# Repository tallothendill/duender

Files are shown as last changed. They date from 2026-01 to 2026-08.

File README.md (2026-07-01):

<!-- Improved compatibility of back to top link: See: https://github.com/othneildrew/Best-README-Template/pull/73 -->

<!--
*** Thanks for checking out the Best-README-Template. If you have a suggestion
*** that would make this better, please fork the repo and create a pull request
*** or simply open an issue with the tag "enhancement".
*** Don't forget to give the project a star!
*** Thanks again! Now go create something AMAZING! :D
-->

<!-- PROJECT SHIELDS -->
<!--
*** I'm using markdown "reference style" links for readability.
*** Reference links are enclosed in brackets [ ] instead of parentheses ( ).
*** See the bottom of this document for the declaration of the reference variables
*** for contributors-url, forks-url, etc. This is an optional, concise syntax you may use.
*** https://www.markdownguide.org/basic-syntax/#reference-style-links
-->
<!--
[![Contributors][contributors-shield]][contributors-url]
[![Forks][forks-shield]][forks-url]
[![Stargazers][stars-shield]][stars-url]
[![Issues][issues-shield]][issues-url]
[![Unlicense License][license-shield]][license-url]
[![LinkedIn][linkedin-shield]][linkedin-url]
-->

<!-- PROJECT LOGO -->
<br />
<div align="center">
  <a href="https://www.printables.com/model/1300968-duender-mgn9h-2x-creality-ender-3-corexy-convertio">
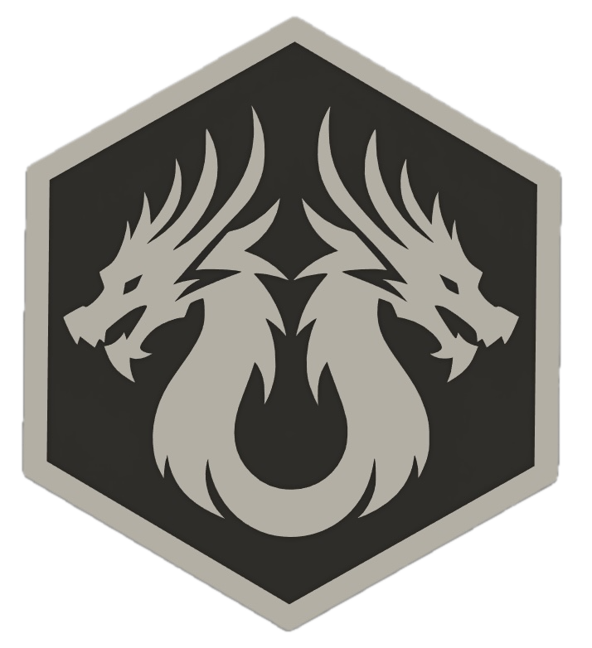
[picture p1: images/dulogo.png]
    
  </a>

  <h3 align="center">Duender mods, triple Z and more...</h3>
  <p align="center">
    Some thougths and mods for the duender project here.
    <br />Note: this is NOT an official repo, Irbis3D repo is <a href="https://github.com/Irbis3D">HERE</a>. Thanks.
  </p>
  <p>
    The Duender project is created and developped by Irbis3D <a href="https://discord.com/channels/1341676245171048473/1354698746524598312">Discord server</a>
  </p>
    <!--
    <br />
    <br />
    <a href="https://github.com/tallothendill/duender/tree/71d104ec3dbbbacea63be96e859a8f34e3e835fc/Kinematic%203Z%20-%20in%20progress">Triple Z axis, with kinematic bed</a>
    </p>X
    &middot;
    <a href="https://github.com/tallothendill/duender/tree/c5b984b065c5a199969d3fe1e7d17b98502cc63b/mods">Mods & stl related to the duender manual</a>
    &middot;
    <a href="https://github.com/othneildrew/Best-README-Template/issues/new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">Request Feature</a>
  </p>
</div>
-->

<!-- TABLE OF CONTENTS -->

<!--
<details>
  <summary>Table of Contents</summary>
  <ol>
    <li>
      <a href="#about-the-project">About The Project</a>
      <ul>
        <li><a href="#built-with">Built With</a></li>
      </ul>
    </li>
    <li>
      <a href="#getting-started">Getting Started</a>
      <ul>
        <li><a href="#prerequisites">Prerequisites</a></li>
        <li><a href="#installation">Installation</a></li>
      </ul>
    </li>
    <li><a href="#usage">Usage</a></li>
    <li><a href="#roadmap">Roadmap</a></li>
    <li><a href="#contributing">Contributing</a></li>
    <li><a href="#license">License</a></li>
    <li><a href="#contact">Contact</a></li>
    <li><a href="#acknowledgments">Acknowledgments</a></li>
  </ol>
</details>
-->

<!-- ABOUT THE PROJECT -->
<!--
## About The Project

[![Product Name Screen Shot][product-screenshot]](https://example.com)

There are many great README templates available on GitHub; however, I didn't find one that really suited my needs so I created this enhanced one. I want to create a README template so amazing that it'll be the last one you ever need -- I think this is it.

Here's why:
* Your time should be focused on creating something amazing. A project that solves a problem and helps others
* You shouldn't be doing the same tasks over and over like creating a README from scratch
* You should implement DRY principles to the rest of your life :smile:

Of course, no one template will serve all projects since your needs may be different. So I'll be adding more in the near future. You may also suggest changes by forking this repo and creating a pull request or opening an issue. Thanks to all the people have contributed to expanding this template!

Use the `BLANK_README.md` to get started.

<p align="right">(<a href="#readme-top">back to top</a>)</p>

### Built With

This section should list any major frameworks/libraries used to bootstrap your project. Leave any add-ons/plugins for the acknowledgements section. Here are a few examples.

* [![Next][Next.js]][Next-url]
* [![React][React.js]][React-url]
* [![Vue][Vue.js]][Vue-url]
* [![Angular][Angular.io]][Angular-url]
* [![Svelte][Svelte.dev]][Svelte-url]
* [![Laravel][Laravel.com]][Laravel-url]
* [![Bootstrap][Bootstrap.com]][Bootstrap-url]
* [![JQuery][JQuery.com]][JQuery-url]

<p align="right">(<a href="#readme-top">back to top</a>)</p>
-->

<!-- GETTING STARTED -->
<!--
## Getting Started

This is an example of how you may give instructions on setting up your project locally.
To get a local copy up and running follow these simple example steps.

### Prerequisites

This is an example of how to list things you need to use the software and how to install them.
* npm
  ```sh
  npm install npm@latest -g
  ```

### Installation

_Below is an example of how you can instruct your audience on installing and setting up your app. This template doesn't rely on any external dependencies or services._

1. Get a free API Key at [https://example.com](https://example.com)
2. Clone the repo
   ```sh
   git clone https://github.com/github_username/repo_name.git
   ```
3. Install NPM packages
   ```sh
   npm install
   ```
4. Enter your API in `config.js`
   ```js
   const API_KEY = 'ENTER YOUR API';
   ```
5. Change git remote url to avoid accidental pushes to base project
   ```sh
   git remote set-url origin github_username/repo_name
   git remote -v # confirm the changes
   ```

<p align="right">(<a href="#readme-top">back to top</a>)</p>
-->

<!-- USAGE EXAMPLES -->
<!--
## Usage

Use this space to show useful examples of how a project can be used. Additional screenshots, code examples and demos work well in this space. You may also link to more resources.

_For more examples, please refer to the [Documentation](https://example.com)_

<p align="right">(<a href="#readme-top">back to top</a>)</p>
-->

<!-- ROADMAP -->
<!--
## Roadmap

- [x] Add Changelog
- [x] Add back to top links
- [ ] Add Additional Templates w/ Examples
- [ ] Add "components" document to easily copy & paste sections of the readme
- [ ] Multi-language Support
    - [ ] Chinese
    - [ ] Spanish

See the [open issues](https://github.com/othneildrew/Best-README-Template/issues) for a full list of proposed features (and known issues).

<p align="right">(<a href="#readme-top">back to top</a>)</p>
-->

<!-- CONTRIBUTING -->
<!--
## Contributing

Contributions are what make the open source community such an amazing place to learn, inspire, and create. Any contributions you make are **greatly appreciated**.

If you have a suggestion that would make this better, please fork the repo and create a pull request. You can also simply open an issue with the tag "enhancement".
Don't forget to give the project a star! Thanks again!

1. Fork the Project
2. Create your Feature Branch (`git checkout -b feature/AmazingFeature`)
3. Commit your Changes (`git commit -m 'Add some AmazingFeature'`)
4. Push to the Branch (`git push origin feature/AmazingFeature`)
5. Open a Pull Request

### Top contributors:

<a href="https://github.com/othneildrew/Best-README-Template/graphs/contributors">
  <img src="https://contrib.rocks/image?repo=othneildrew/Best-README-Template" alt="contrib.rocks image" />
</a>

<p align="right">(<a href="#readme-top">back to top</a>)</p>
-->

<!-- LICENSE -->
<!--
## License

Distributed under the Unlicense License. See `LICENSE.txt` for more information.

<p align="right">(<a href="#readme-top">back to top</a>)</p>
-->

<!-- CONTACT -->
<!--
## Contact

Your Name - [@your_twitter](https://twitter.com/your_username) - email@example.com

Project Link: [https://github.com/your_username/repo_name](https://github.com/your_username/repo_name)

<p align="right">(<a href="#readme-top">back to top</a>)</p>
-->

<!-- ACKNOWLEDGMENTS -->
<!--
## Acknowledgments

Use this space to list resources you find helpful and would like to give credit to. I've included a few of my favorites to kick things off!

* [Choose an Open Source License](https://choosealicense.com)
* [GitHub Emoji Cheat Sheet](https://www.webpagefx.com/tools/emoji-cheat-sheet)
* [Malven's Flexbox Cheatsheet](https://flexbox.malven.co/)
* [Malven's Grid Cheatsheet](https://grid.malven.co/)
* [Img Shields](https://shields.io)
* [GitHub Pages](https://pages.github.com)
* [Font Awesome](https://fontawesome.com)
* [React Icons](https://react-icons.github.io/react-icons/search)

<p align="right">(<a href="#readme-top">back to top</a>)</p>
-->

<!-- MARKDOWN LINKS & IMAGES -->
<!-- https://www.markdownguide.org/basic-syntax/#reference-style-links -->
<!--
[contributors-shield]: https://img.shields.io/github/contributors/othneildrew/Best-README-Template.svg?style=for-the-badge
[contributors-url]: https://github.com/othneildrew/Best-README-Template/graphs/contributors
[forks-shield]: https://img.shields.io/github/forks/othneildrew/Best-README-Template.svg?style=for-the-badge
[forks-url]: https://github.com/othneildrew/Best-README-Template/network/members
[stars-shield]: https://img.shields.io/github/stars/othneildrew/Best-README-Template.svg?style=for-the-badge
[stars-url]: https://github.com/othneildrew/Best-README-Template/stargazers
[issues-shield]: https://img.shields.io/github/issues/othneildrew/Best-README-Template.svg?style=for-the-badge
[issues-url]: https://github.com/othneildrew/Best-README-Template/issues
[license-shield]: https://img.shields.io/github/license/othneildrew/Best-README-Template.svg?style=for-the-badge
[license-url]: https://github.com/othneildrew/Best-README-Template/blob/master/LICENSE.txt
[linkedin-shield]: https://img.shields.io/badge/-LinkedIn-black.svg?style=for-the-badge&logo=linkedin&colorB=555
[linkedin-url]: https://linkedin.com/in/othneildrew
[product-screenshot]: images/screenshot.png
[Next.js]: https://img.shields.io/badge/next.js-000000?style=for-the-badge&logo=nextdotjs&logoColor=white
[Next-url]: https://nextjs.org/
[React.js]: https://img.shields.io/badge/React-20232A?style=for-the-badge&logo=react&logoColor=61DAFB
[React-url]: https://reactjs.org/
[Vue.js]: https://img.shields.io/badge/Vue.js-35495E?style=for-the-badge&logo=vuedotjs&logoColor=4FC08D
[Vue-url]: https://vuejs.org/
[Angular.io]: https://img.shields.io/badge/Angular-DD0031?style=for-the-badge&logo=angular&logoColor=white
[Angular-url]: https://angular.io/
[Svelte.dev]: https://img.shields.io/badge/Svelte-4A4A55?style=for-the-badge&logo=svelte&logoColor=FF3E00
[Svelte-url]: https://svelte.dev/
[Laravel.com]: https://img.shields.io/badge/Laravel-FF2D20?style=for-the-badge&logo=laravel&logoColor=white
[Laravel-url]: https://laravel.com
[Bootstrap.com]: https://img.shields.io/badge/Bootstrap-563D7C?style=for-the-badge&logo=bootstrap&logoColor=white
[Bootstrap-url]: https://getbootstrap.com
[JQuery.com]: https://img.shields.io/badge/jQuery-0769AD?style=for-the-badge&logo=jquery&logoColor=white
[JQuery-url]: https://jquery.com 
-->

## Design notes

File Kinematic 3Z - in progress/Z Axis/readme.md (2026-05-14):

<p>
  Aligned the Lead screw axis with the GE5C bearing axis to eliminate torque creation while moving.
  <br />The screw must create the movement, the rail is only a guide, the GE5C is only carrying the weight of the bed vertically.
</p>

<p>The most important point in building this is to give the bed holders some degrees of freedom:
<ul>
  Front left holder to front bed extrusion:
    <li>No freedom, act as a reference point</li>
    <li>Have the two M5 screw/M5T-nut secured so the holder does not move in X, Y or Z</li>
</ul>
<ul>
  Front right holder to front bed extrusion:
  <li>Allows for movement in X axis</li>
  <li>This allows for the bed to tilt laterally, and for X axis thermal expansion without forcing the bed to warp under stress</li>
  <li>The screws must be tight to the point where there is no more Z rattling, but the T-nuts still slide into the extrusion channel</li>
</ul>
<ul>
  Back support to back bed extrusion:
    <li>Allows for movement both in X and Y axis</li>
    <li>This allows for the bed to tilt front to back, and therml expansion without Y axis stress</li>
    <li>Here also, the screws must be tightened just enough to eliminate any rattling in Z direction, but still slide laterally in the extrusion channel and also on the Y axis (the support should &quot;glide&quot; onto the extrusion a few 0.x mm)</li>
</ul>
</p>
<p>
  A good way to &quot;calibrate&quot; screw torques is to tighten them to contact, then, while manually making the bed tilt back and forth, tightening/loosening by 1/8 turn until it feels just right: the bed should tilt every direction without notable resistance point.
</p>

<p>
  Any comments or improvements are welcome at:<br />
 <a target="_blank" href="https://discord.com/channels/1341676245171048473/1451586393146003507">B&W ender MGN9H build log on Discord</a>
</p>

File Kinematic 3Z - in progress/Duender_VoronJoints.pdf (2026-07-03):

## Blind joints “a la Voron“ ADDON ⁻ All versions

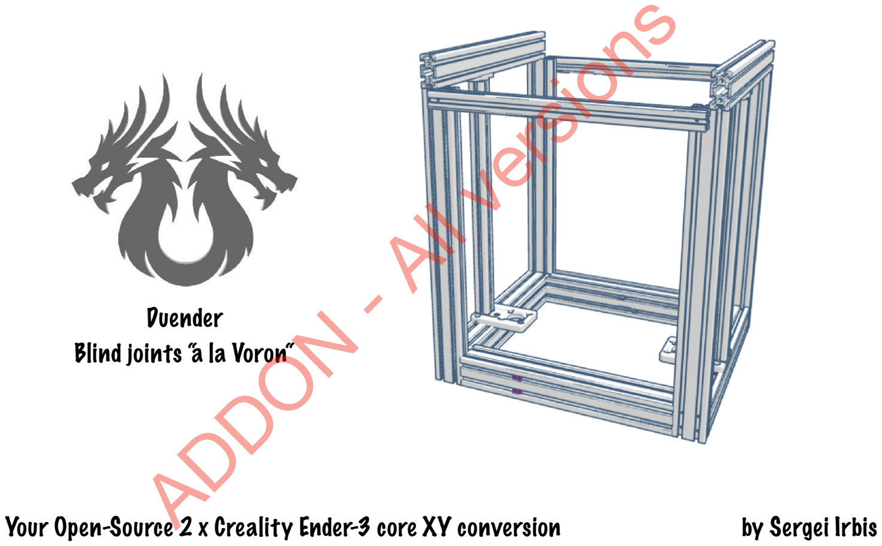
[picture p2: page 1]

## Duender

Your Open-Source 2 x Creality Ender-3 core XY conversion | by Sergei Irbis

## Caution!

For this method to work, the cuts on your extrusions must be perfectly square with their body.
If the cut is not 90°, the assembly cannot end square!
You can somewhat compensate with a shim where needed, but this solution has its limits, plus it may create unwanted gaps between your extrusions.

two printed parts to help with the process:

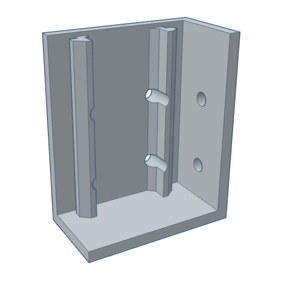
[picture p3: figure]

A simple drilling jig, to place the holes without too much thinking.
Many models exist online, some even with bearings to guide you.

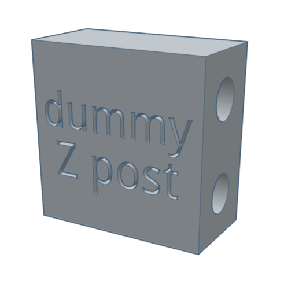
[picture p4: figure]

A 40x40x20mm dummy to fill the space of 2040 vertical extrusions.
Its holes allow for two M5x45 SHCS Ender 3 screws to secure it onto 4040 extrusions sides.

TOOLS YOU’LL NEED:

2mm Allen key

A drill, I went with a 4,2mm bit, but if you are precise enough, 4mm should be fine.
Note that a drill press will make things way easier, as it is important to drill straight and square into the extrusions.

A M5 tap, along with its handle, and some lubricant to cut the threads into the extrusions channels.

Base structure | 6

## Assembling the frame

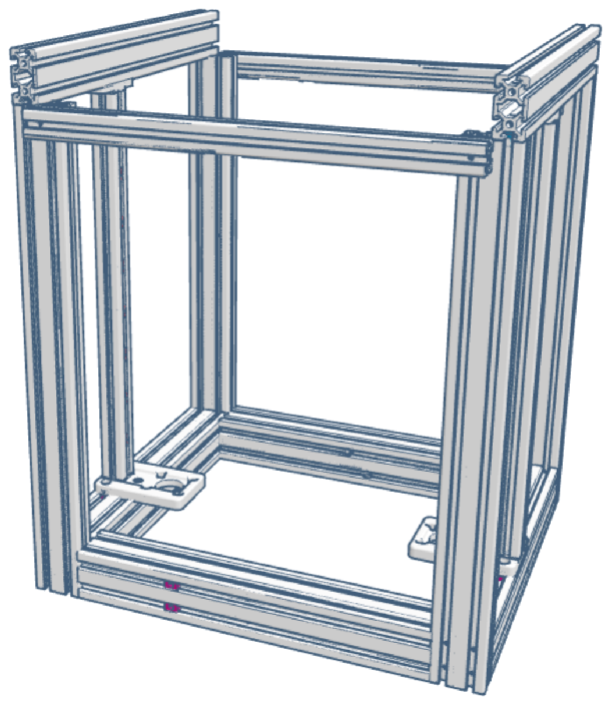
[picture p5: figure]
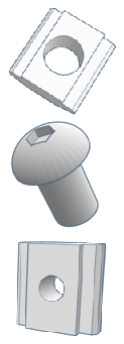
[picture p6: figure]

M5 T-slot nut | 18
M5x8 BHCS screw | 54
M3 T-slot nut | 16

Base structure | 7

2020-D *

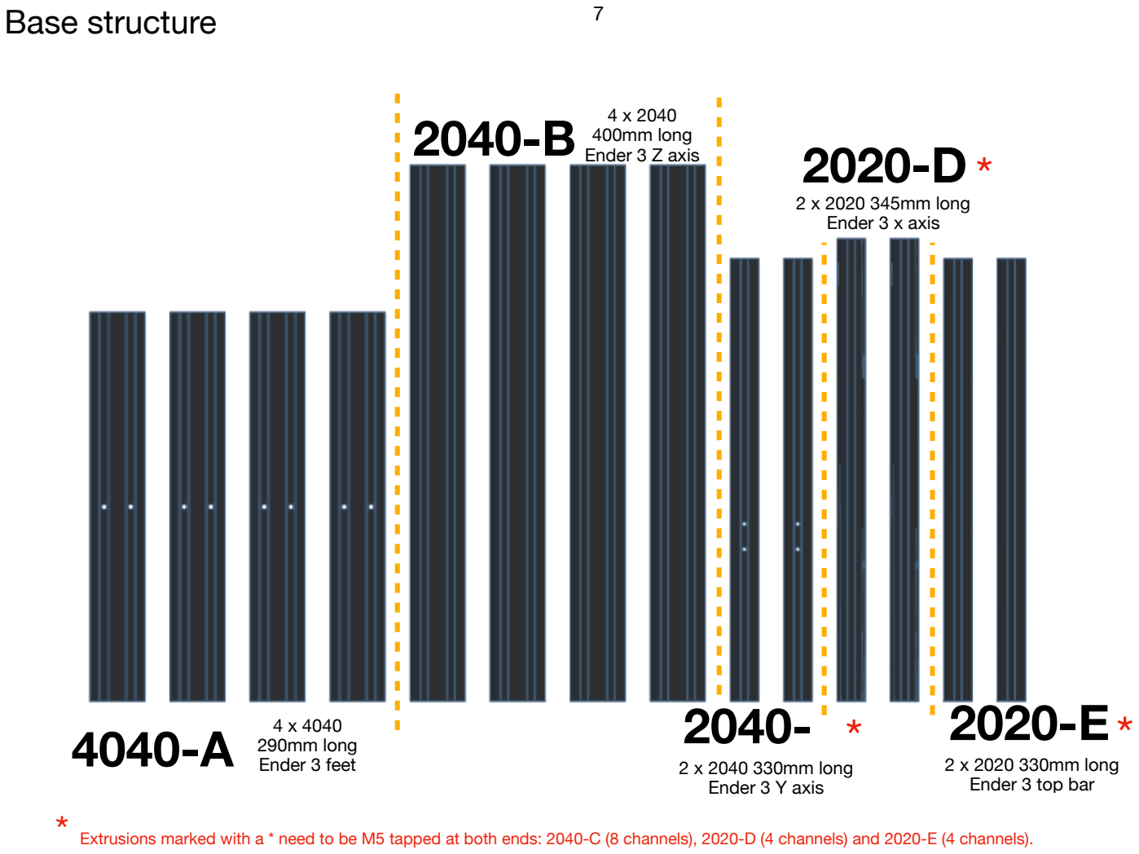
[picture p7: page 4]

4 x 2040
400mm long 2040-B Ender 3 Z axis

4 x 4040
290mm long 4040-A Ender 3 feet | 2 x 2040 330mm long
| Ender 3 Y axis

2040- *

2 x 2020 345mm long
Ender 3 x axis

2 x 2020 330mm long
Ender 3 top bar

2020-E*

* Extrusions marked with a * need to be M5 tapped at both ends: 2040-C (8 channels), 2020-D (4 channels) and 2020-E (4 channels).

Base structure | 8

Drill the 400mm 2040 Z posts bases
2 holes in the 20mm side, 4 holes in the 40mm face.

Bottom holes have their centre at 10mm from the base, Top holes are centred at 30mm from the base.

Of course, all are centred on the extrusions channels. Be precise when marking or centre-punching those.

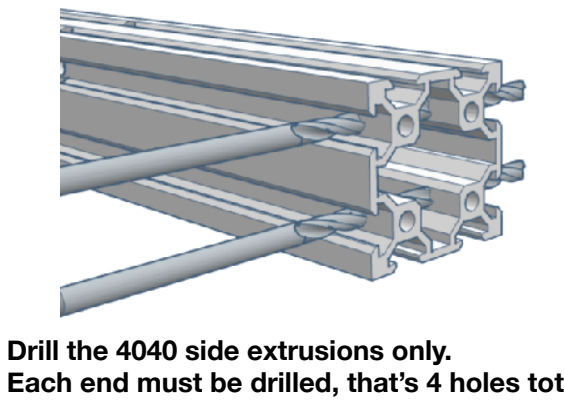
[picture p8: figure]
Drill the 4040 side extrusions only.

Each end must be drilled, that’s 4 holes total.

The front and back 4040 remain untouched.

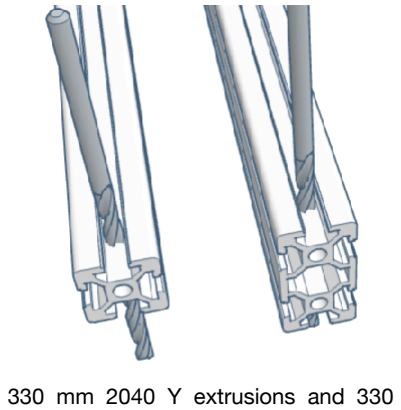
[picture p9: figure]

Same dimensions and requirements here. | The 330 mm 2040 Y extrusions and 330 mm
| 2020-E extrusions only need one hole on each
| end (10mm from the end).

Base structure | 9

Tap all the 4040 extrusions channels with a M5 bit. 4 extrusions, 4 holes on each side, that’s 32 threaded holes total.
You will also need to tap the 400mm 2040 channels (16 total), the 330mm 2040 channels (8 more), the 345mm 2020 extrusions (4), and one of the 330mm 2020 (only 2 here). Yes, that’s a lot.

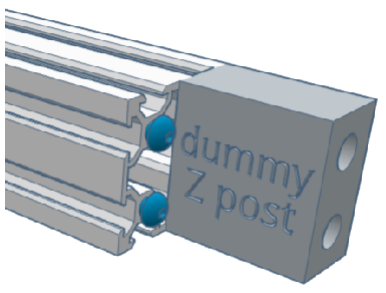
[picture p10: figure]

Use the dummy Z post, with two M5x45 screws from the ender 3 frame, and attach it in the front side of the front 4040 extrusion.
Two M5x8 BHCS are inserted in the innermost channels, almost fully seated.

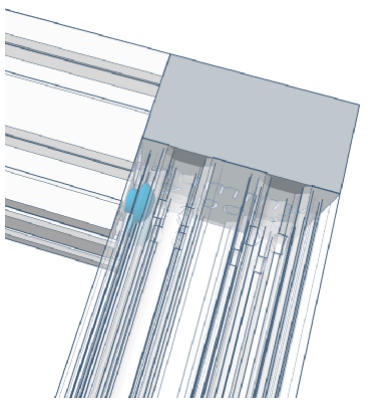
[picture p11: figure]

The dummy serves as a stop when sliding the side 4040 onto the BHCS heads.

Press the 4040 as far and flush as possible.

Base structure | 10

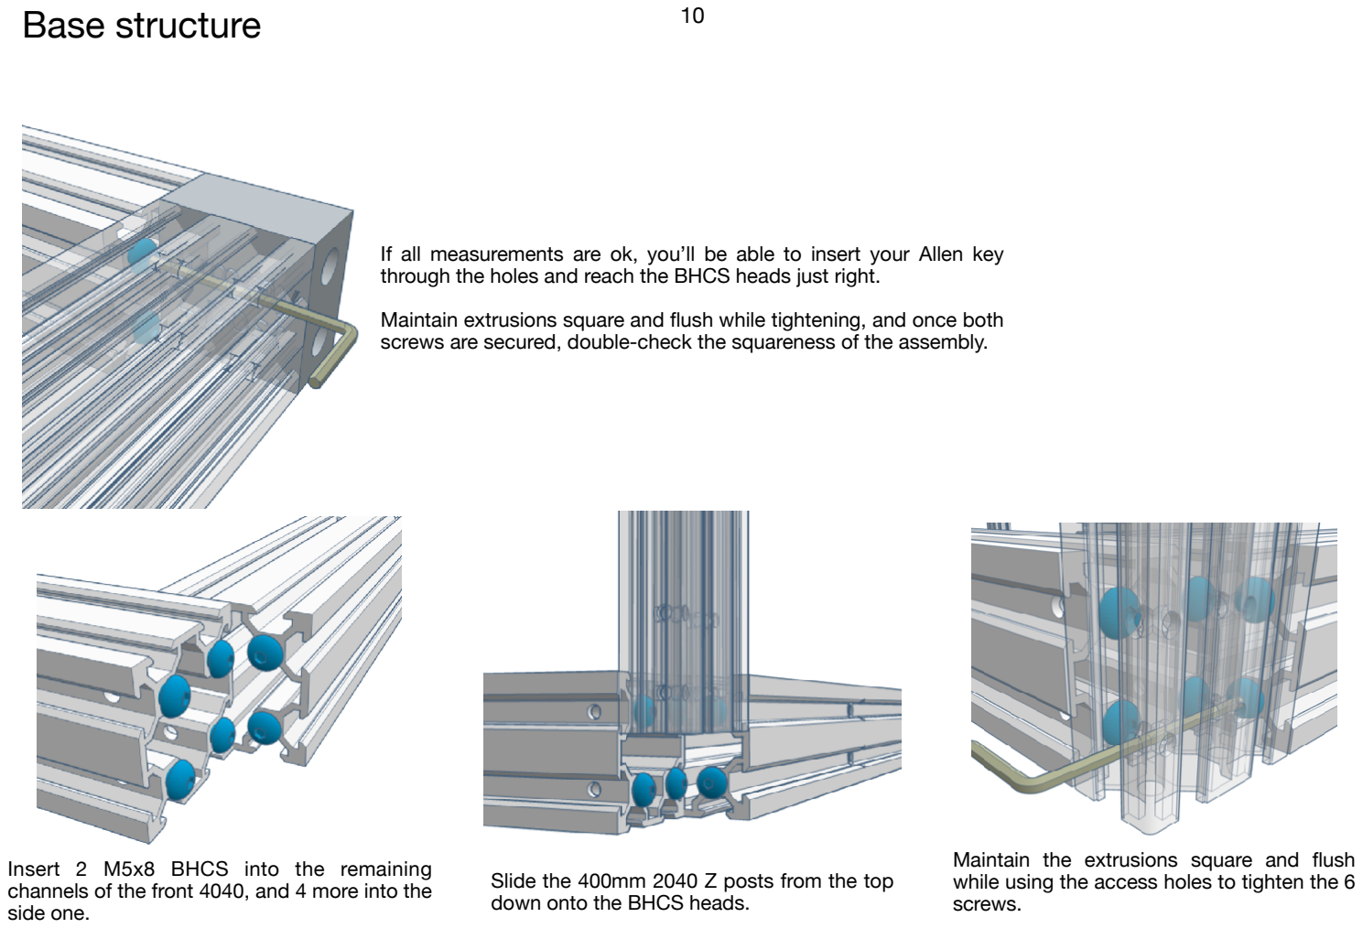
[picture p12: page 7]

If all measurements are ok, you’ll be able to insert your Allen key through the holes and reach the BHCS heads just right.

Maintain extrusions square and flush while tightening, and once both screws are secured, double-check the squareness of the assembly.

Insert 2 M5x8 BHCS into the remaining channels of the front 4040, and 4 more into the side one.

Slide the 400mm 2040 Z posts from the top down onto the BHCS heads.

Maintain the extrusions square and flush while using the access holes to tighten the 6 screws.

Base structure | 11

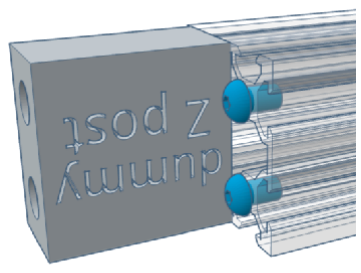
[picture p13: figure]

Continue by screwing the dummy on the
opposite side of the 4040 front extrusion, and

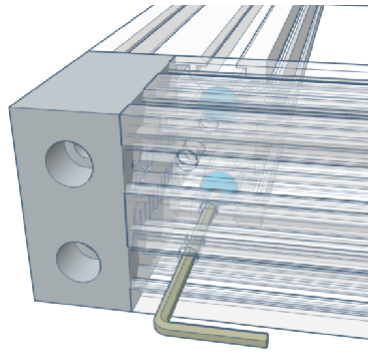
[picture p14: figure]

inserting 2 M5x8 BHCS in the inside channels | Insert the side 4040 to press against the dummy,
| and proceed with tightening the screws once
| everything is flat and flush.

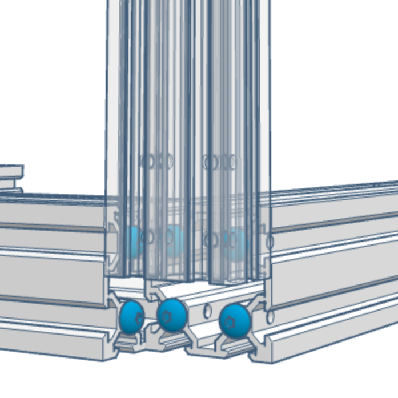
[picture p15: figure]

Same as before, insert 6 M5x8 BHCS in the channels once you got the dummy out, insert the front right 2040 by the top and proceed to squaring and assembly

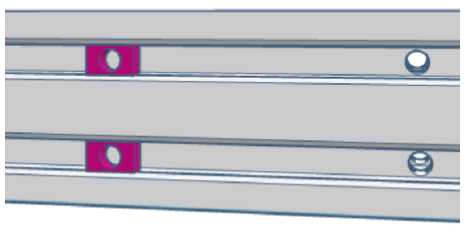
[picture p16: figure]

Slide 2 M5 T-slot nuts in the front channels as pictured

Slide 2 M5 T-slot nuts in the outer top channel and 1 M5 T-slot nut in the inner one of both side extrusion as pictured
(6 M5 T-slot nuts total)

Base structure | 12

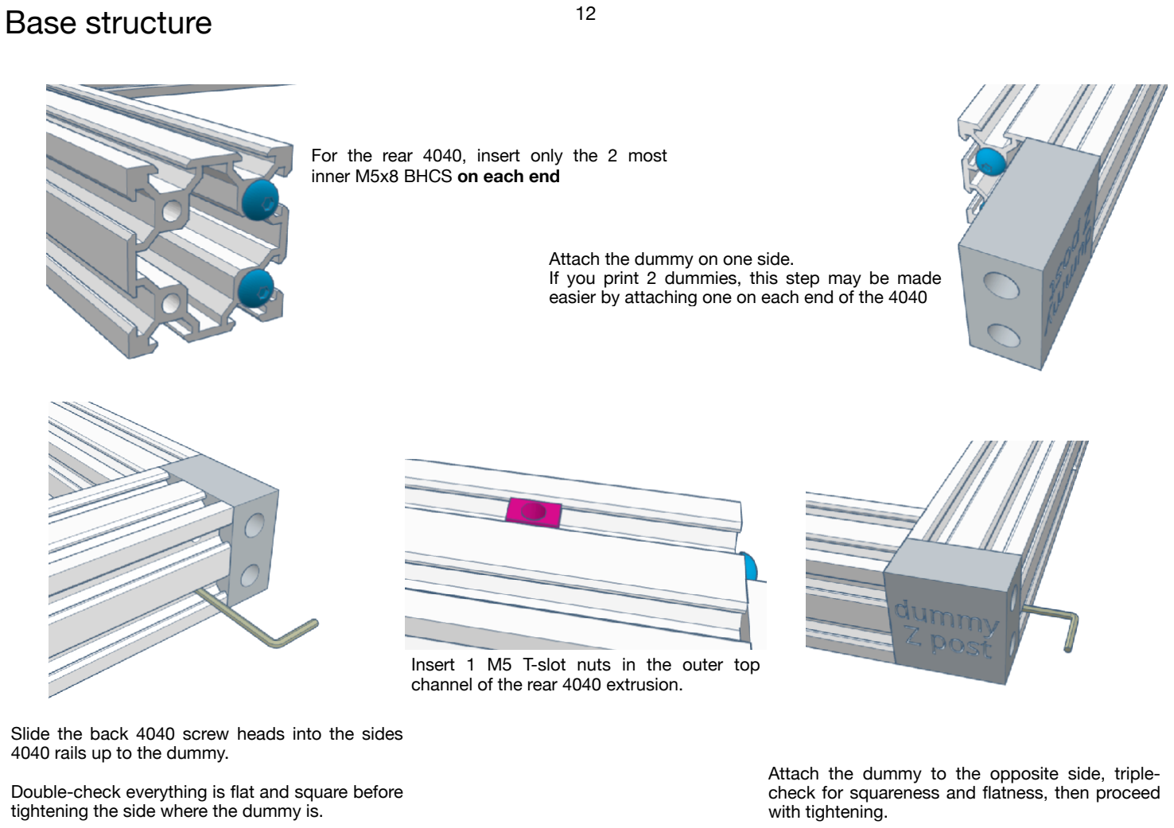
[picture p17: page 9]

For the rear 4040, insert only the 2 most inner M5x8 BHCS on each end

Attach the dummy on one side.
If you print 2 dummies, this step may be made easier by attaching one on each end of the 4040

Slide the back 4040 screw heads into the sides 4040 rails up to the dummy.

Double-check everything is flat and square before tightening the side where the dummy is.

Attach the dummy to the opposite side, triple-check for squareness and flatness, then proceed with tightening.

Insert 1 M5 T-slot nuts in the outer top channel of the rear 4040 extrusion.

Base structure | 13

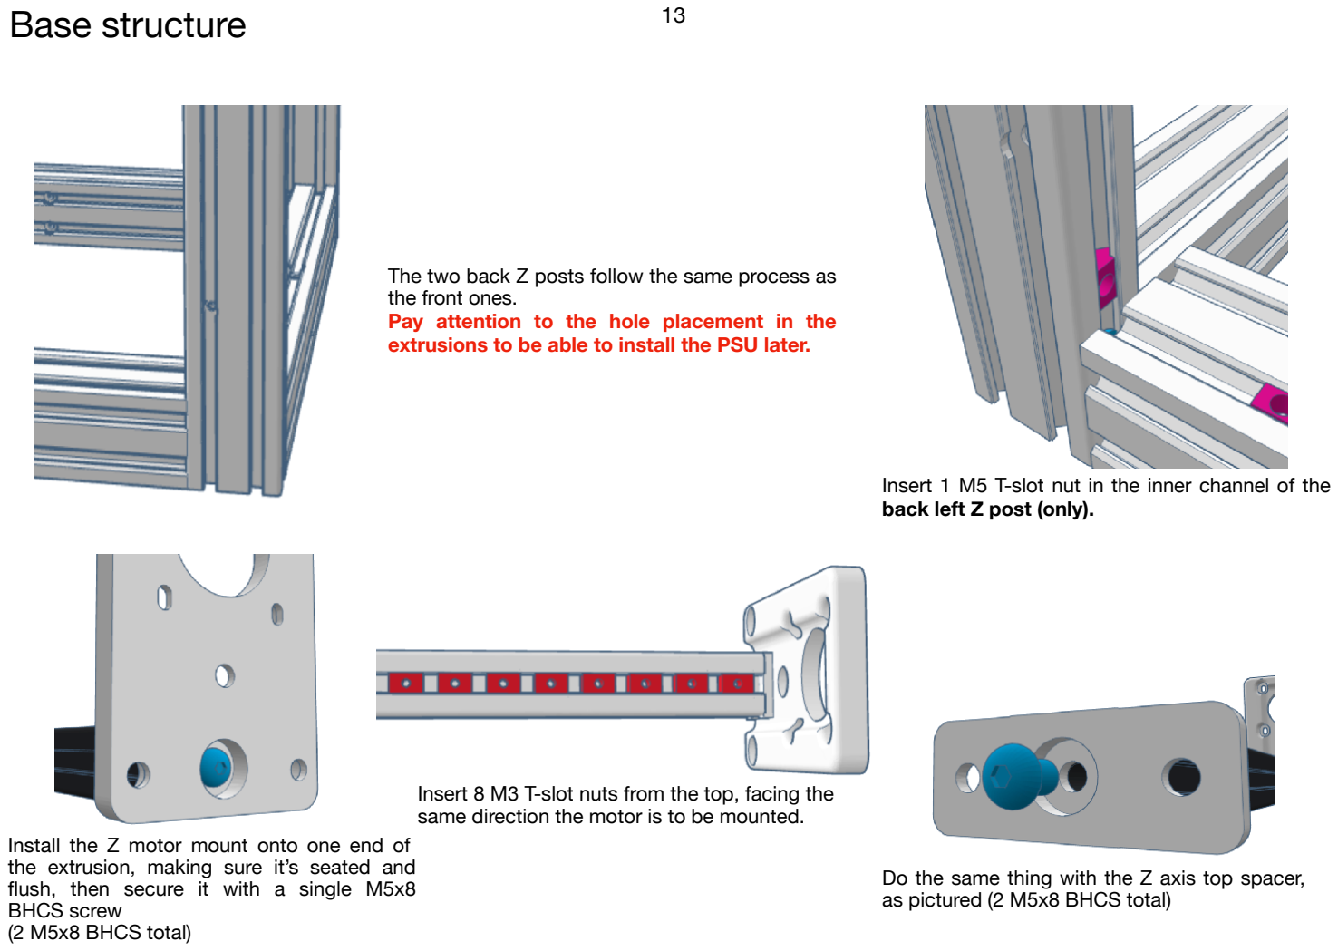
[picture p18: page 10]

The two back Z posts follow the same process as the front ones.
Pay attention to the hole placement in the extrusions to be able to install the PSU later.

Insert 1 M5 T-slot nut in the inner channel of the back left Z post (only).

Install the Z motor mount onto one end of the extrusion, making sure it’s seated and flush, then secure it with a single M5x8 BHCS screw
(2 M5x8 BHCS total)

Do the same thing with the Z axis top spacer, as pictured (2 M5x8 BHCS total)

Insert 8 M3 T-slot nuts from the top, facing the same direction the motor is to be mounted.

Base structure | 14

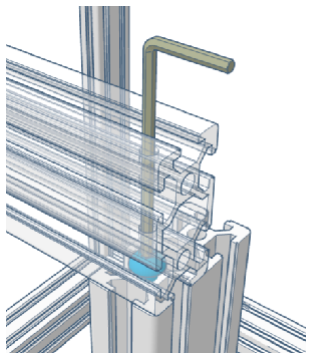
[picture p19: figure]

You should then be able to slide the 330mm 2040 Y extrusions onto the screw heads, and once you are sure they are flush, tighten them in.

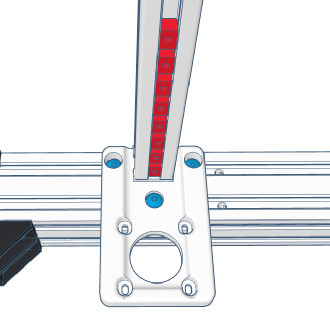
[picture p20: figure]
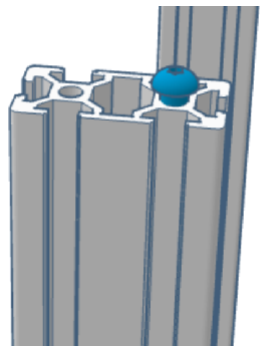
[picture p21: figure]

Once the Z-axis assemblies are aligned, insert 1 M5x8 BHCS on top of the outer channel of each 400mm Z post.

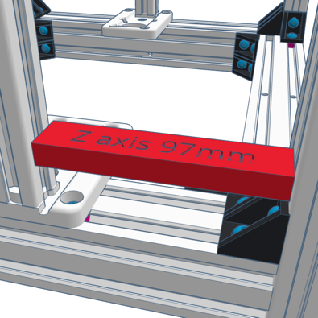
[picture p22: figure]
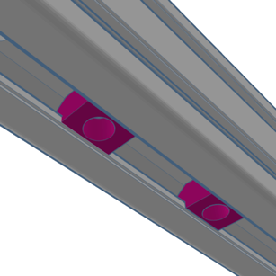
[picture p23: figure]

Slide 2 M5 T-slot nuts on the underside of each 330mm 2040 Y axis
(4 M5 T-slot nuts total)

Install the Z axis onto one side of the base
Align the previously installed M5 T-slot nuts with the holes Secure it with three M5x8 BHCS screws (6 M5x8 BHCS total)
DO NOT FULLY TIGHTEN THE SCREWS YET The assembly needs to be able to slide side to side

Use the 3D printed spacer provided in the tools or a calliper to adjust the Z axis 97mm from the front post, then tighten the 3 M5x8 BHCS screws of the base This is the default distance. You may need to adjust this distance later, depending on your toolhead configuration

Base structure | 15

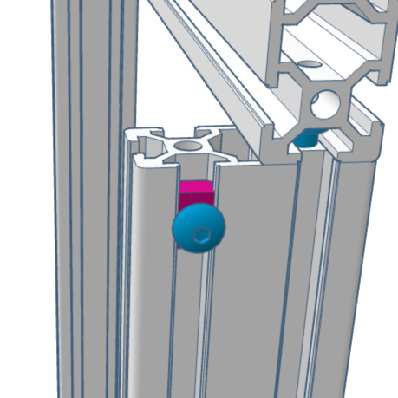
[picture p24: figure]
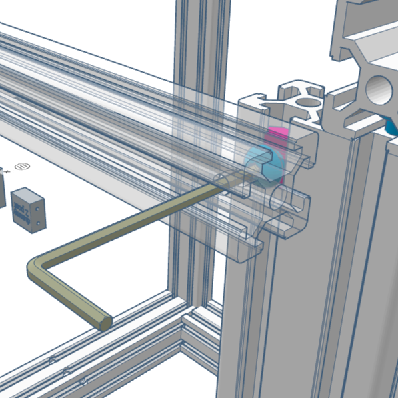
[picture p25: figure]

Slide a M5 BHCS + M5 T-slot nut assembly
into the outer rail of each back 400mm 2040 Z post

You can now use the access hole into the 330mm 2020-E back brace to secure it to the back of the frame.
Make sure it’s level, flat and centred.

Repeat those last 2 steps for the front brace.

Do one last check from every angle and corner to ensure everything is square, straight, flush, level, you name it, and you’re good to go.

Align the 2 M5 T-slot nuts remaining under the 2040-C with the top Z axis plate, and use 2 M5x8 BHCS screws to secure it

Check the distance to the front post to be 97mm all along the Z axis before tightening the screws

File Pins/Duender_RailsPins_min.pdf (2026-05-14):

## Duender

Your Open-Source 2 x Creality Ender-3 core XY conversion | by Sergei Irbis

## Some points of the build require your attention

## Linear rails handling

Once the printer is complete, the print bed and the nozzle will be heating and may cause severe burning if you are not cautious.
Do not touch those parts while in function.

A risk of overheating or electric short in components is always possible. In some cases, this could lead to the printer starting a fire.
Please, double check your build and babysit your printer during the tuning phase as well as its first jobs
Keeping an extinguisher near those appliances is a good practice.

Read the full doc before starting your build, and do not hesitate to reach out on the Discord server (https://discord.com/channels/1341676245171048473/1354698746524598312) to ask for help any time you are unsure

The rail axis carriages are meant to slide smoothly with very little resistance.

Be very careful they do not fall off the rail, as this would most likely result in irreparable damage.

When you receive them, they are very often covered in some kind of protective oil.
The video below by Canuck Creator offers all the advice you need to clean and lubricate your rails.

The MGN9H rails are quite thin and can be somewhat difficult to fit onto V-slot extrusions.
You can use some 3D printed helpers to align them: use spacers (https://www.printables.com/model/641406-v-slot-shim-adapters-mgn7-mgn9-positioning/files) or tools like this (https://www.printables.com/model/998923-2040-aluminum-extrusion-mgn9-alignment-tool) or this. (https://www.printables.com/model/450861-mgn9-mgn12-linear-rail-2020-alignment-tools)
Try tightening the screws progressively along the rail while maintaining alignment until all screws are secured.

https://2cm.es/1mI5J (https://youtu.be/UYvhYjkBFTY?si=c9C3WkopiexPDw9c)

# Table of contents

Hardware reference | 1
Bill of materials | 2
Important tips | 4
Assembling the frame | 6
Z gantry | 17
AB gantry | 22
X axis gantry | 29
Dragonburner toolhead | 34
Power supply, control box and screen housing | 45
Wiring | 48
A few words about Medusa HC project | 55

https://2cm.es/1lYzA

https://2cm.es/1h2CE

https://2cm.es/1h2CJ

Need more information? | Wanna support the project? If you enjoy Duender and want to support what I do, there are a few ways to help: Patreon — monthly support https://patreon.com/Irbis3D Ko-fi / Buy Me a Coffee — one-time donations https://buymeacoffee.com/Irbis3D YouTube Super Thanks — under any video https://youtube.com/@Irbis3D Your support helps me create more content, upgrade gear, and keep experimenting with cool ideas. Thank you.

Sergei Irbis.

Know your bits | 1

## Hardware reference

BHCS (Button Head Cap Screw)

Metric fastener with hemispheric head and hex drive. Mostly used with M5 T-slot nuts

T-slot nut

Nut that is inserted inside the slot of aluminium extrusions. Must be inserted on beforehand
Hammerhead T nuts can be used after assembly

FHCS (Flat Head Cap Screw)

Metric fastener with cone shaped head and flat top

Hex nut

Coupled with a screw to create a bolt. Nylstop ones have a plastic insert to prevent them un-tightening

Heat set insert

Once heated with the soldering iron, it melts into plastic, which makes a tight fit by solidifying.
M3 threading, 5mm outer diam., 4mm long.

Toothed idler

Has bearings in the center bore, used to redirect the belt in the motion system. GT2 refers to the belt pitch between teeth

Shim (or spacer)

Metal flat ring, with a set thickness, used as spacer between parts and bearings. Not to be confused with washers

Pin

Smooth precision-cut metal rod used as an idler axle.

Toothless idler

Similar idler without teeth, for the smooth side of the belt. 16T is for teeth count, 6W for belt width, 3B for axis bore diameter

SHCS (Socket Head Cap Screw)

Metric fastener with cylindrical head and hex drive. Mostly used with T-slot nuts.

BOM and sourcing | 2

## Bill of materials

Fasteners | Qty | Order | Affiliated link / Notes | Kinematics | Qty | Order | Affiliated link / Notes
M5x25 SHCS | 2 | ✓ | From Ender 3 | 42-34 Nema17 motor | 2 | ✓ | From Ender 3
M4X35 FHCS | 4 | ✓ | From Ender 3 | 42-40 Nema17 motor | 2 | ✓ | From Ender 3
M4x20 SHCS | 2 | ✓ | From Ender 3 | Leadscrew T8x8mm 365mm | 2 | ✓ | From Ender 3
M4 hex nut | 4 | ✓ | From Ender 3 | Motor coupler D5x8 Optional elastic coupler | 2 2 | ✓ | From Ender 3
Metal corner bracket | 28 | | https://s.click.aliexpress.com/e/_c4DUW5sX
M5x8 BHCS | 92 | | | T8 Lead screw | 2 | ✓ | From Ender 3
M5 T-slot nut | 79 | | https://s.click.aliexpress.com/e/_c4EDoXzD | Leadscrew brass nut Optional anti backlash nut | 2 2 | ✓ | From Ender 3
M5 hex nut | 2
M3x30 BHCS | 14 | | | Y plate | 1 | ✓ | From Ender 3
M3x20 BHCS | 4 | | | 10t Nema 14 motor | 1 | | https://s.click.aliexpress.com/e/_c4NfNSaf
M3x18 BHCS | 8 | | | MGN9H or MGN12H 300mm rail | 5 | | https://s.click.aliexpress.com/e/_oFYW0St
M3x16 BHCS | 2 | | | GT2 6mm wide belt | 5m | | https://s.click.aliexpress.com/e/_ooDLTEH
M3x14 BHCS | 2 | | | Pulley GT2 16T 6W 5B | 2 | | https://s.click.aliexpress.com/e/_c4mjCdxl
M3x12 BHCS | 9 | | | Toothless idler GT2 16T6W3B | 10 | | https://s.click.aliexpress.com/e/_c3Fqpe71
M3x8 BHCS | 74 | | | Toothed idler GT2 16T6W3B | 2 | | https://s.click.aliexpress.com/e/_c3Fqpe71
M3x6 BHCS | 24 | | | M3x20mm pin | 3 | | https://s.click.aliexpress.com/e/_c4CXA4ZN
M3 T-slot nut | 40 | | https://s.click.aliexpress.com/e/_c4EDoXzD | M3x30mm Pin | 8 | | https://s.click.aliexpress.com/e/_c4CXA4ZN
M3 hex nut | 13 | | | M3x0.5mm shim | 38 | | https://s.click.aliexpress.com/e/_c4BNsuvz
M3 heat set insert | 44 | | https://s.click.aliexpress.com/e/_c4DbNkaX | M3x10mm spacer | 6 | | https://s.click.aliexpress.com/e/_c3rUz3wF

Long screws kit: https://s.click.aliexpress.com/e/_c4VYXcQR (colour: Button head)
Short screws kit: https://s.click.aliexpress.com/e/_c30o44Xt

BOM and sourcing | 3

## Are you planning for Medusa HC?


Medusa HC is a toolhead changer specifically designed for
the Duender offering by default 4 swappable hotends.
If you use a different control board, with for example a
Raspberry Pi as your Klipper host, you may have to add a
second board to get enough hotend heaters and thermistors
ports available.
However, if you are considering using the BTT Manta 5P
recommended here, and planning for Medusa HC, it is
advised to switch it right away for a BTT Manta 8P V2.0 with
a CB2 card and the TMC2209 drivers so you can expand and
connect the hotends with no added modification.
BTT Manta 8P V2.0 wiring is detailed in the Medusa HC guide

Electronics | Qty | Order | Affiliated link / Notes

24V 15A PSU, housing, switch, cable | 1 | ✓ | From Ender 3

Heatbed 24V 235x235mm | 1 | ✓ | From Ender 3

4010 24V axial fan | 2 | ✓ | From Ender 3

BTT HDMI5 V1.2 | 1 | | https://s.click.aliexpress.com/e/_c4odBUeJ

BTT Manta 5P BTT Manta 8P V2.0 | 1 1 | | https://s.click.aliexpress.com/e/_oktZaKt

BTT CB2 | 1 | | https://s.click.aliexpress.com/e/_oDMokmp

BTT TMC 2209 | 5 | | https://s.click.aliexpress.com/e/_oktZaKt

Misc | Qty | Order | Affiliated link / Notes

Duender print settings:

2020 V-slot extrusion 300mm | 1 | | Unless you plan for Medusa HC, see p.16 first

Material: ABS or ASA for all load-bearing parts
Electronics box and display holder can be printed
in any material
Layer height: 0.2mm

12mm silicone bed spacer Optional Spring bed spacer | 4 4 | ✓ | From Ender 3

Bambulab X1/PIP hotend | 1 | | https://s.click.aliexpress.com/e/_c3yvXGSr
3010 24V axial fan | 1 | | https://s.click.aliexpress.com/e/_c3YNV2ux
4010 24V radial fan | 2 | | https://s.click.aliexpress.com/e/_c3eDwMjh
Sherpa mini Thumbscrew w/Spring | 1 | | https://s.click.aliexpress.com/e/_c4kf7lXN
Sherpa mini filament gear | 1
Sherpa mini idler gear | 1
Wires, connectors, pins, crimping pliers and stuff

No. of walls/top/bottom layers: 5

Infill: > 50% (60% recommended) for load bearing parts
Gyroid for strength, cross-hatch for speed.
Can be as low as 15% for electronics or screen
boxes

Last minute call | 4

## Important tips

## Ender 3 disassembly

DO NOT DISMANTLE THE POWER SUPPLY. You will use the PSU along with its cover, the power switch and the wire ending with an XT60 plug.

Deconstruction is easier if you first remove all connections from the mainboard. Those are held with hot glue, carefully remove it with a pair of pliers. You can pull out the X axis after removing the top bar, which simplifies deconstruction. The X motor has a QR code sticker hiding four screws.
The 4040 central profile and plastic parts won't be needed. Remove the rubber feet for easier squaring, but you may want to put them back later.

Depending on your revision, you may have to take the Ender 3 motors pulleys off. Some use a printed tool, (https://www.printables.com/model/230013-press-fit-pulley-extractor-for-nema-17) some just Dremel them out. Be careful!

## Linear rails

This manual depicts MGN9H build on the images, however, it also applies to MGNH12 builds as the steps, hardware and procedures are the same. Be careful however and make sure you do print the right parts for your build.

## Z Axis

It is probably a good idea, to replace the Z motors shaft couplers with "spring motor coupler" ones at approx. 2x€2.50. In the same domain, it is advised to replace original brass lead screw nuts with anti-backlash spring loaded ones at approx. 2x€2.50 too.

## Toolhead

The toolhead of choice is a Dragonburner with a Bambulab X1/P1P series hotend, associated with a Sherpa mini extruder. This will allow for easier switching to Medusa HC should you want to: your carriage, fans, hotend and most extruder parts can then be reused. If you want to go for Medusa HC right away, switch to the relevant manual, and skip the toolhead assembly mentioned here.

## Electronics

if you want to be really frugal, any Klipper board will work, however, the BTT Manta 5P with a CB1/2 is likely the best choice for your Duender. Note that if you plan on building Medusa HC at some point, you would be better off starting with a BTT Manta 8P+CB2 from the beginning, as it offers all the necessary ports for your Duender with Medusa HC attached.

Original design goes with a BTT HDMI5. You may not need a display, as you’ll be able to use the web interface anyway, but the original 12864 of your Ender 3 can do the job, or you can get any other Klipper compatible touch screen (you may need to tweak the config files though).

Remember that you might need different hardware if you made different electronics choices.

Last minute call | 5

## Building

During the frame assembly, it is crucial that everything ends up square and flush.The base and four vertical posts should be placed first then squared while gradually tightening the fasteners. It is tedious but the print quality of your Duender depends on it.

Since MGN9H rails are about as wide as the V-slots, it's not easy to get them centred. You can print some spacers (https://www.printables.com/model/641406-v-slot-shim-adapters-mgn7-mgn9-positioning/files) or alignment tool like this (https://www.printables.com/model/998923-2040-aluminum-extrusion-mgn9-alignment-tool) or this. (https://www.printables.com/model/450861-mgn9-mgn12-linear-rail-2020-alignment-tools)

The belt tensioners are also quite fiddly since you need to get all washers and idlers lined up before putting the pin in. A printed jig (https://www.printables.com/model/1500832-duender-belt-tensioner-jig) may help you.

If you are unsure about how to correctly tap your extrusions, check out this video first:

https://2cm.es/1lYBi

Base structure | 6

## Assembling the frame


Metal corner bracket | 28
M5 T-slot nut | 71
M5x8 BHCS screw | 70
M3 T-slot nut | 16

Base structure | 7

2020-D *

4 x 2040
400mm long 2040-B Ender 3 Z axis

4 x 4040
290mm long 4040-A Ender 3 feet | 2 x 2040 330mm long
| Ender 3 Y axis

2040-C*

2 x 2020 345mm long
Ender 3 x axis

2 x 2020 330mm long
Ender 3 top bar

2020-E*

* Extrusions marked with a * need to be M5 tapped at both ends: 2040-C (8 channels), 2020-D (4 channels) and the back 2020-E (2 channels).

Base structure | 8

Insert 2 M5 T-slot nuts in both the 2040-B (8 M5 T-slot nut total)

Make sure to orient the back 2040B extrusions so the mounting holes for the power supply are towards the inside of the printer (see picture on next page)

Place 2 brackets and
insert the M5x8 screws

Repeat the process at
the opposite end of
each 4040-A
(16 M5x8 BHCS total)

First, prepare each 4040-A side with 11 M5 T-slot nut as shown here You can keep the original Ender 3 plastic pads as feet on the underside (22 M5 T-slot nuts total)

Base structure | 9

Make sure everything is flush and square before final tightening

Once done, repeat the same steps with the remaining 4040-A and the two 2040-B to form the opposite side of the frame

Make sure the holes for the power supply end on the inside of the back 2040-B

Insert a M5 T-slot nut in the inside slot of each 2040-B post of the previous assemblies
(4 M5 T-slot nuts total)

Base structure | 10


Place the 4040-A flush and square to one side assembly and proceed installing the brackets with 6 M5x8 screws on each end
(24 M5x8 BHCS total)

Repeat those steps in the four corners of the base

Once done, double check all your alignments

It’s a good idea to measure each diagonal of the base square to make sure they are equal too!

Insert 6 M5 T-slot nut in each of the remaining 4040-A part as shown here (12 total)
Add the M5 T-slot nuts shown in picture in the relevant extrusions (so 15 total)

Front 4040-A only (screen housing)

Back 4040-A only (electronics box)

Base structure | 11

Carefully tap each end of the channel in both the 2020-D extrusions with an M5 bit

Install the Z motor mount onto one end of the extrusion, making sure it’s seated and flush, then secure it with a single M5x8 BHCS screw
(2 M5x8 BHCS total)

Do the same thing with the Z axis top spacer, as pictured
(2 M5x8 BHCS total)

Insert 8 M3 T-slot nuts from the top, facing the same direction the motor is to be mounted. (16 M3 T-slot nuts total)

Base structure | 12

Install the Z axis onto one side of the base
Align the previously installed M5 T-slot nuts with the holes
Secure it with three M5x8 BHCS screws
(6 M5x8 BHCS total)

DO NOT FULLY TIGHTEN THE SCREWS YET The assembly must remain free to slide side-to-side for later adjustments.


You can 3D print a 97mm spacer, or use a calliper to adjust the Z axis spacing from the front post, then tighten the 3 M5x8 BHCS screws of the base

This is the default distance. You may need to adjust this distance later, depending on your toolhead configuration

Base structure | 13

Once done, insert 4 M5 T-slot nut on the underside of each one
(8 M5 T-slot nuts total)

Insert an M5 T-slot nut on the top of each post, in the outside rail as shown
(4 M5 T-slot nut total)
Place the 2040-C on top of each side

Make sure the extrusions are flush at each end then proceed and install the corner brackets

Repeat those steps on the other side to assemble the second Y axis to the frame
(8 M5x8 BHCS total)

Align the 2 M5 T-slot nuts remaining under the 2040-C with the top Z axis plate, and use 2 M5x8 BHCS screws to secure it
(4 M5x8 BHCS total)
Check the distance to the front post to be 97mm all along the Z axis before tightening the screws

Check whether the channels of your 2040-C extrusions are already tapped If not carefully tap each one on each end of both extrusions with an M5 bit (8 channels total).

Base structure | 14

Carefully tap each end of the channel in the back 2020-E extrusion with an M5 bit


Insert one M5 T-slot nut at the top of each rear Z posts
(2 M5 T-slot nut total)

For the rear right Z post only: add a second M5 T-slot nut (for the electronics box later on)

Align the 2020-E extrusion flush to the top of the Z posts The 2020-E must be centred between the posts Align the T-slot nuts
Install a corner bracket with 2 M5x8 BHCS screws
(4 M5x8 BHCS total)

Once done, insert 2 M5 T-slot nuts into the back rail, and 2 more into the front one
(4 M5 T-slot nuts total)

Base structure | 15

Insert one M5 T-slot nut at the top of each front Z posts (2 M5 T-slot nut total)

Align the last 2020-E extrusion flush to the top of the Z front posts
The 2020-E must be centred between the posts Align the T-slot nuts
Install a corner bracket with 2 M5x8 BHCS screws (4 M5x8 BHCS total)

For the front brace, insert 2 M5 T-slot nuts into the back rail

Base structure | 16

The freshly bought 300 mm long extrusion is to be used to build the X axis, a few sections later.

NOTE that if you are planning for MedusaHC mod later, the front brace needs to be 350mm long.

So the best solution is probably to cut the 2020-E front brace to 300mm and use it for your X axis, and buy directly the 350mm 2020 extrusion for the Medusa HC front brace (or buy both 350 and 300mm if you prefer not to cut your extrusions).

Use a suitable metal cutting saw blade, Dremel bit or other adapted tool to make a clean cut

Assembling the Z axis | 17

## Z gantry

Lead screw nut | 2
(from Ender 3)
8mm lead screw | 2
(from Ender 3)
Motor shaft coupler | 2
(from Ender 3)
M4x35 FHCS | 4
(from Ender 3)
Nema 17 42-34 | 2
(from Ender 3)

Assembling the Z axis | 18


Start by placing one linear rail, MGN9H or MGN12H, on both side Z axis and secure it with 8 M3x8 BHCS every other hole (16 M3x8 BHCS total).
You should use a plastic jig to center the rail on the extrusion especially if you are using MGN9H rails.

Base of the rail is at 25mm distance from the bottom of the extrusion.

Take extra precaution so the carriage does not fall off the rail: place plastic plugs, use tape, whatever works for you.

Place the Z motors under their plates and use 4 M3x8 BHCS screws to secure them
(8 M3x8 BHCS total)
Orient the motor plug to the back of the printer

Assembling the Z axis | 19

Install the lead screw nuts under the plastic bed holders, and insert 2 M3x12 BHCS screws (you can also use the ones originally coming from your Ender 3)
(4 M3x12 BHCS total)

If your lead screws aren’t perfectly straight, it is advised you replace them with some "anti-backlash" ones, to avoid Z wobble


Turn the bed holders around being careful not to lose the screws and secure them with M3 nuts. (4 M3 Hex nut total)

Alternatively, you could insert 2 M3 heat-set inserts (not accounted in the bom) from the top, and tighten the M3 screws from bottom.

Install the lead screws couplers onto the Z motors shafts and tighten only the lower screw

If your lead screws aren’t perfectly straight, you may want to replace those with "spring" or "elastic" ones to avoid Z-wobble

Assembling the Z axis | 20

Insert the lead screws into the lead screws nut from the top then rotate them until fully seated into the couplers

Tighten the upper screw of the coupler to hold the lead screw

Place each bed holder onto its rail carriage and use 4 M3x8 BHCS screws to attach it
(8 M3x8 BHCS total)


Mind the orientation: the longer arm goes towards the front of the printer.

Assembling the Z axis | 21

Place the Ender 3 Y plate onto the bed holders, 4 silicone spacers -here 12mm shown in orange (you may use the springs from the Ender 3) then the heatbed

Of course, the wiring of the heatbed should end towards the back of your printer

Use the original 4 M4x35 FHCS screws and secure them under the bed holders with M4 nuts


(4 M4x35 FHCS and 4 M4 hex nut total)

Building the AB kinematics | 22

## AB gantry

M5 T-slot nut | 2
M3 Heat set insert | 12
M3x0.5 spacer | 26
M3x10 spacer | 2
Nema 17 42-40 | 2
(from Ender 3)

GT2 16T6W3B toothless idler 8

GT2 16T6W5B motor pulley 2

M5 Nylstop nut | 2
(from Ender 3)
MGN9H 300mm rail | 2
or MGN12H 300mm rail
M3 T-slot nut | 16
M3x30 pin | 4
M3x8 BHCS screw | 24
M3x30 BHCS screw | 8
M3x6 BHCS screw | 4
M5x8 BHCS screw | 12
M3x20 pin | 2

Building the AB kinematics | 23

Prepare the bottom part of AB motor holders: 4 heat-set inserts each side
(8 M3 heat-set inserts total)

Install the motors under the plates with 4 M3x8 BHCS screws in the 4 corners
Mind the motor plug orientation
(8 M3x8 BHCS total)

Also place the motor pulleys onto the shafts of A & B motors
Do not tighten their set screws too much. They will need to be adjusted after belts installation

Carefully press-fit two M3x30mm pins into their holes, making sure to keep them straight up
(4 M3x30mm pins total)

Building the AB kinematics | 24


For the Right AB mount:

Stack
2 M3x0.5mm spacers,
1GT2 16T 6mm toothless idler,
2 M3x0.5mm spacers,
1 GT2 16T 6mm toothless idler,
2 M3x0.5mm spacers onto the outer most pin.

Stack
2 M3x0.5mm spacers,
1 GT2 16T 6mm toothless idler,
1 M3x0.5mm spacer,
1 M3x10mm spacer on the inner-most pin.

When the motors are one against another, the idlers should be perfectly level between both sides. If that is not the case, adjust the shims count as necessary

For the Left AB mount:

Stack
2 M3x0.5mm spacers,
1 GT2 16T 6mm toothless idler,
2 M3x0.5mm spacers,
1 GT2 16T 6mm toothless idler,
2 M3x0.5mm spacers onto the outer most pin.

Stack
1 M3x10mm spacer,
1 M3x0.5mm spacer,
1 GT2 16T 6mm toothless idler,
2 more M3x0.5mm spacers on the inner-most pin.

The best option is certainly to buy and install a metal M3x10 spacer, but should you not have one on hand, you may use the printed one provided in the stl files.

Building the AB kinematics | 25

Slide a M5 T-slot nut in each Y axis and install the AB motor holders using a M5x8 BHCS screw
(2 M5 T-slot nuts and 2 M5x8 BHCS total)

Use 2 M5x8 BHCS screws to hold into the tapped end of the 2040-C Y axis and another one to hold onto the back brace M5 T-slot nut (6 M5x8 BHCS total)

Place the top half of the AB motors mount on each side, carefully inserting the M3x30 pins top into their slots.
Attach them with 4 M3x30 BHCS for each side (8 M3x30 BHCS total)

Building the AB kinematics | 26


Slide the T-slot nuts into the top of each Y extrusion, aligning them one after another, all the way to the AB motor holders. Use a centring 3D printed jig to center them and slightly tighten the screws, just enough to hold the rail in place.

DO NOT FULLY TIGHTEN THE SCREWS YET

Install 8 M3 T-slot nuts, one every other hole, securing them with 8 M3x8 BHCS screws through the rail. Leave them quite loose for now.
(16 M3 T-slot nut and 16 M3x8 BHCS total)

Building the AB kinematics | 27

Install the front holders with 2 M5x8 BHCS screws each side
(4 M5x8 BHCS total)

Mind the orientation, the holders are not symmetrical

Prepare both the Bottom_Left and Bottom_Right belt tensioners by placing 2 M3 heat-set inserts in the top holes (4 M3 heat-set inserts total).

Insert an M5 Nylstop nut into the groove inside both holders. A small dab of glue may help keep them in place
(2 M5 hex nut total).

Press-fit the M3x20mm pins into each side slot, making sure they go square (2 M3x20mm pins total)

Building the AB kinematics | 28

Stack 2 M3x0.5mm shims, a 16mm toothless idler and 2 M3x0.5mm shims onto each pin (8 M3x0.5 shims and 2 GT2 16T6W3B toothless idlers).

Carefully place the Top_Left and Top_Right parts onto their pins and use 2 M3x6 BHCS screws each side to secure the assembly (4 M3x6 BHCS total)


Set the two tensioners aside, it will be way easier to install them with the belts.

Building the X axis | 29

## X axis gantry

M5 T-slot nut | 6
M5x8 BHCS screw | 6
M3 T-slot nut | 8
M3 Heat set insert | 6
MGN9H 300mm rail | 1
MGN12H 300mm rail
M3x0.5 spacer | 12 | GT2 16T6W3B toothless idler 2
M3x30 pin | 4 | GT2 16T6W3B toothed idler 2
M3x8 BHCS screw | 8
M3x6 BHCS screw | 8
M3x30 BHCS screw | 6
M3x10 spacer | 4

Building the X axis | 30

Prepare both bottom parts of the X carriage with 3 heat-set inserts each side
(6 M3 heat-set inserts total).

Place each part onto its rail carriage and attach them with 4 M3x6 BHCS screws each side
(8 M3x6 BHCS total)

Carefully press-fit the M3x30 pins into their slots, keeping them square to the base
(4 M3x30mm pins total)

Building the X axis | 31


Insert 8 M3 T-slot nuts into the front of the 300mm 2020 extrusion, the last rail, and secure the assembly with

For the left hand side:
Left-most pin:
- 1 M3x10mm spacer,
- 1 M3x0.5mm shim,
- 1 toothless idler,
- 2 M3x0.5mm shims
Right-most pin:
- 2 M3x0.5mm shims,
- 1 toothed idler,
- 1 M3x0.5mm shim,
- 1 M3x10mm spacer

For the right hand side:
Left-most pin:
- 1 M3x10mm spacer,
- 1 M3x0.5mm shim,
- 1 toothed idler,
- 2 M3x0.5mm shims
Right-most pin:
- 2 M3x0.5mm shims,
- 1 toothless idler,
- 1 M3x0.5mm shim,
- 1 M3x10mm spacer

Building the X axis | 32

Place the X axis onto both carriages

on the back side and 2 more under the

Insert 2 M5 T-slot nuts on the top side, 2

extrusion

Carefully push the top halves onto the M3x30 pins.

Secure each carriage with 3 M3x30 BHCS screws

Center and secure the X extrusion with 3 M5x8 BHCS on each end: one on the top, one on the back and one under the extrusion.

(6 M3x30 BHCS and 6 M5x8 BHCS total)

Building the X axis | 33

Finally, slide the X axis back and forth several times so the Y rails align themselves
Gradually tighten the M3x8 screws each side from one end to another to lock the rails in place

Toolhead assembly | 34

## Dragonburner toolhead

Dragonburner

Why this toolhead?
All this hardware will be reused for MedusaHC. If you are building for Medusa, please refer to the relevant manual for your toolhead.

Toolhead assembly | 35

Prepare the top part of the carriage with 2 M3 heat-set inserts.

Remember to break the top front support piece.

Use 2 M3x8 BHCS to attach the top and bottom parts together.


Set the carriage aside, it will be used when installing the belts
(use 4 M3x6 BHCS to attach it to the X rail).

Toolhead assembly | 36

Place 4 M3 heat-set inserts in the back of the toolhead cowling.

Break the supports on the side of the hotend support

Install 2 M3 heat-set inserts into the top holes of the hotend support.
Add 2 M3 heat-set inserts to the side, in the holes that were covered by the supports.

Install 2 M3 heat-set inserts into the top holes of the extruder adapter plate.

Toolhead assembly | 37

Install the Bambulab X1 series hotend with its heatsink under the hotend support.

Mind the orientation of the heatsink

Slide the hotend support with the hotend into the back of the cowling, then use 2 M3x12 BHCS from the front to secure it.

Use 2 M3x20 BHCS to lock the hotend in place

Press-fit the 3010 axial fan into the front of the cowling
Remember to route the wires towards the back.

Toolhead assembly | 38


Press-fit the 2 4010 radial fans in each side of the cowling, from back to front.

Keep the wiring out towards the back.

Place the extruder support on top of the hotend, behind the cowling, and pass 2 M3x20 BHCS screws to hold it.

Drop 1 M3 hex nut into its slot.

You may want to hold it with a drop of glue, in that case, temporarily add a screw from the back to hold the nut in place while the glue cures.

Toolhead assembly | 39

https://github.com/Annex-Engineering/Sherpa_Mini-Extruder/tree/master/Build_Instructions

Now is the time to build your Sherpa mini extruder.

Its author provides an excellent assembly manual.

Download it from the GitHub linked below, proceed with the build, then come back for the last assembly steps.

Place your newly assembled extruder on top of the Dragonburner.

Use 2 M3x14 BHCS to attach the Sherpa mini to the extruder plate.


After completing the next section and installing the belts, your toolhead will attach to its carriage from the back, with 2 M3x8 BHCS on the bottom, and 1 M3x12 BHCS at the top.

A & B belts installation | 40

"Equal belt tension is important to the proper function of a CoreXY motion system.

We recommend to run one belt to get the required length, remove the belt from the printer and cut the second belt to the exact same length.

As both belt paths have the same length this is an easy way of getting a consistent tension."

- The Voron team
GT2 6mm belt | approx. 2x1,5m
M5x25 SHCS | 2
(from Ender 3)

A & B belts installation | 41

## A belt

Pass the belt into the L side tensioner (flat side against idler) then insert the tensioner into the L front holder, and secure it with a M5x25 SHCS screw passing from the front of the holder


Pass the short side of the belt into the toothed idler and towards the X axis toolhead carriage

The longer side passes next to the left Y carriage all the way to the AB motor holder at the back left
Use the lower idler to turn 90° and head to the right AB motor holder

A & B belts installation | 42

1: Into the right AB motor holder, use the first idler to redirect the belt towards the motor pulley (not shown here)
2: Place the belt into the A motor pulley, it’s time to adjust pulley height. Then back to the second idler (the lower one) to
3: continue towards the front of the printer

Finally, use the lower idler inside the right Y axis carriage to turn 90° and head to the right side of the printhead carriage

You will need to use whichever toolhead carriage you have chosen to hold both extremities of the belt

Use the toolhead carriage to temporarily clamp the belt. Use 4 M3x6 BHCS to install it onto the rail carriage.

Once secured, cut the belt to the correct length, and unmount it to use as reference

Place the freshly cut A belt on top of the remaining GT2 length and make sure they stay perfectly flush (you can tape them together) Cut the second belt at the exact dimension: matching teeth count now ensures matching tension later

You can now reinstall the A belt with the same exact procedure you just followed

A & B belts installation | 43

## B belt


Pass the belt into the R side tensioner (flat side against idler) then insert the tensioner into the R front holder, and secure it with a M5x25 SHCS screw passing from the front hole of the holder

Pass the short side of the belt into the toothed idler and towards the X axis toolhead carriage

The longer side passes next to the right Y carriage all the way to the AB motor holder at the back right
Use the upper idler to turn 90° and head to the left AB motor holder

A & B belts installation | 44

Use the X carriage to clamp the belts, by loosening slightly, tensioning the belts, and tightening it back.

IMPORTANT: Double check that both belts are perfectly level and straight all along their path

If that is not the case, you may need to adjust the number of M3x0.5mm spacers used to level the idlers

Also check for the A and B motors pulleys height. You may have to unscrew them a bit to align them with the belts
It may be a good idea to add a drop of blue threadlocker to the set screws of the pulleys before final tightening

Finally, use the upper idler inside the left Y axis carriage to turn 90° and head to the left side of the printhead carriage

You will need to use whichever toolhead carriage you have chosen to hold both extremities of the belt

1: Into the left AB motor holder, use the first idler to redirect the belt towards the motor pulley (not shown here)
2: Place the belt into the B motor pulley, it’s time to adjust pulley height. Then back to the second idler (the upper one)
3: continue towards the front of the printer

PSU, control box & screen | 45

## Power supply, control box and screen housing


M5x8 BHCS screw | 8
M3 Heat set insert | 8
M4x20 SHCS | 2
(from Ender 3)
24V 15A PSU | 1
(from Ender 3)
BTT HDMI5 V1.2 | 1

PSU, control box & screen | 46

Prepare the bottom of the electronics box by inserting 8 heat-set inserts, one into each corner hole, and on the inside mainboard pillars

Use original M4x20 SHCS screws to attach the original power supply to the back left 2040-B Z post

Place the electronics box in the back lower right corner of the frame, and use the two remaining M5 T-slot nuts to secure it with 2 M5x8 BHCS screws

Box shown is for BTT Manta 5p mainboard. You may need a different model depending on your configuration

PSU, control box & screen | 47


Mount the completed screen housing to the front of your Duender using the last two remaining M5 T-slot nuts with 2 M5x8 BHCS screws

Start by inserting your BTT HDMI5 screen into the frame.
The rear speaker and the buttons indicate the correct orientation.

Place the assembly onto the main support part, and attach the screen from the underside with 4 M3X8 BHCS screws.

Mainboard installation | 48

## Wiring


This section is intended for the BTT Manta 5P mainboard loaded with a CB1/CB2
If you are building Medusa right away, please check M8P wiring and setup in the MHC manual.

You will find all the information you need on the BTT Wiki: https://2cm.es/1lYBC (https://global.bttwiki.com/M5P.html)
Files and firmware can be downloaded from the GitHub: https://2cm.es/1h2DL (https://github.com/bigtreetech/Manta-M5P/)

Keep in mind you may need to extend or completely remake some cables, and for this some tools like a soldering iron, good crimping pliers and a set of connectors will prove more than useful

Image from detailed videos about the Manta 5P by Victor Bared Jumpers setup, image install: https://2cm.es/1lYBp (https://youtu.be/Mec3cZnCP18?si=VkWnbPqD_my4Xc08)
Wiring: https://2cm.es/1lYBr (https://youtu.be/LZFxCJQfl8I?si=Z7Ys0Ox6w-WK8Ww8)

Micro-JST connectors some
and pins

Wires in different colours plenty 1 mm², 0.5 mm² etc.

Mainboard installation | 49

## Jumpers basics

TMC2209 UART mode

VBB

VBB

VBB

VBB

VBB

24V motors power

24V 12V 5V

Fan0
Parts cooling fan

Fan1
Hotend fan

Fan
Electronics fan

Fans voltage choices

Wifi antenna plug

Mainboard installation | 50

## Toolhead and heatbed wires

(TB)

Heatbed thermistor

Heatbed heater
(HB)

Parts cooling fans
(Fan0)

Extruder motor
(Motor 5)

Hotend fan
(Fan1)

Hotend thermistor
(TH0)

Heating cartridge
(HE0)


As an example, a Dragonburner toolhead with a Galileo2 extruder and a E3D Voron hotend
However, most toolhead configurations will use the exact same connector types.

Mainboard installation | 51

## Mainboard ports

Green wiring goes to the hotend Blue wiring goes to the heatbed

XT60 cable from Ender 3
24 V DC from power supply

Heating Bed (HB)
No polarity

Bed Thermistor (TB)
No polarity

TMC2209 x 5

Hotend Thermistor (TH0)
No polarity

Hotend heating cartridge (HE0) No polarity

B motor plug (left hand)

A motor plug (right hand)

Z0 motor plug (right hand)

Z1 motor plug (left hand)

Extruder motor plug

HDMI
Usb-A to Usb-C

HDMI5 screen

Mainboard installation | 52

## Going home

You should now be ready to insert your Manta 5P into the electronics control box
Secure it with 4 M3x6 BHCS screws, and go ahead with all your connections

Make good use of all the box cutouts to manage your cables and secure them with zipties or other sleeving of your choice

Temporary jumper to power the board by USB

To flash the image onto the CB1 microSD card, you may need to use the jumper shown here and power the mainboard with 5V by USB cable

Mainboard installation | 53

## (Nearly) Everything you ever wanted to know about Klipper

https://2cm.es/1i1XM (https://www.youtube.com/watch?v=JQFw9zdHB5w) | https://2cm.es/1n0Wo (https://www.youtube.com/watch?v=-e81KhcYGCA)
https://2cm.es/1n0Yt (https://www.youtube.com/watch?v=bj69-lfF6FQ) | https://2cm.es/1i1Yq (https://www.youtube.com/watch?v=mIDtFIi-M4w)

Mainboard installation | 54

## Electronics case fans


Congratulations! Your build is now complete! Next step is installing Klipper and building your printer.cfg file Once your printer is alive, we can only recommend the excellent Ellis’ Print Tuning Guide: https://ellis3dp.com/Print-Tuning-Guide/

## We wish you loads of prints and fun with your Duender!

Once you are all done, use the last 4 M3x6 BHCS screws to close the electronics box

You may want to cool down your electronics with two 4010 axial fans taken from the Ender 3 toolheads

You can use 8 M3x18 BHCS screws with 8 M3 nuts to secure them to the box lid

Electronics fans
(Fan)

Coming soon! | 55

## A few words about Medusa HC project

https://youtu.be/hpV5Z1TnGdY?si=FyJBHvE2mylvz7cY or https://2cm.es/1mI62

What? You want more?
Ok… What if I told you that your Duender can have up to 4 different toolheads? What if you could print 4 different colours or experiment with 4 different materials at the same time, without needing to poop-purge?

Sounds great, doesn’t it? Well stay tuned, because your open-source, budget multi-toolhead mod for the Duender is coming to you.

More info on Irbis 3D channel : https://2cm.es/1h7sX

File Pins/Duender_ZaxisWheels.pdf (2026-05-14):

## V-wheels Z axis ADDON ⁻ “Pins” version


## Duender

Your Open-Source 2 x Creality Ender-3 core XY conversion | by Sergei Irbis

Assembling the Z axis | 16

## Z gantry

Wheel M5 spacer; (from Ender 3); M5 Nylstop nut; Eccentric M5 nut; M5x30 BHCS; M4x35 FHCS; M4 Nylstop nut; Open Build plates; M3 Nylstop nut; 12mm silicone spacers; Nema 17 42-34; M3x16 BHCS; (from Ender 3) 4; M3x8 BHCS

Lead screw nut | 2
(from Ender 3)
8mm lead screw | 2
(from Ender 3)
POM V-Wheel | 8
(from Ender 3)
Motor shaft coupler | 2
(from Ender 3)

Assembling the Z axis | 17

Insert 4 M5x30 BHCS from the underside Spacers go over the smaller holes and

Install the lead screw nuts under the plastic bed holders, and insert 2 M3x16 SHCS or BHCS (Or you can use the ones originally coming from your Ender 3)

If your lead screws aren’t perfectly straight, it is advised that you swap the original lead screw nuts from the Ender 3 with some anti-backlash ones, to avoid Z wobble

eccentric nuts over the larger ones
Those are all from the original Ender 3 roller mounts

and an M5 Nylstop (self-locking) nut

Finally, add 4 V-rollers from your Ender 3,

DO NOT TIGHTEN THE NUTS YET, you need the whole screws/wheels to be loose


Turn the bed holders around being careful not to lose the screws and secure them with M3 nuts

Assembling the Z axis | 18


Place the roller plate behind the bed holder and use 4 M3x8 BHCS to hold it
Secure the screws with 4 M3 nuts


Place the Z motors under their plates and use 4 M3x8 BHCS to secure them. Orient the motor plug to the back of the printer


Install the lead screw shaft couplers onto the Z motor shafts and tighten only the lower screw

If your lead screws aren’t perfectly straight, you may want to replace those with "spring" or "elastic" ones to avoid Z-wobble

Assembling the Z axis | 19


Insert the bed holder assembly onto the Z axis (note that the longer side goes towards the front) and tighten the V-wheels
Once secured, adjust the eccentric nuts to ensure all 4 wheels apply equal pressure


The wheels should rotate smoothly with a slight resistance when turned by hand

Double-check that the screw heads don’t touch the extrusion surface.


Insert each lead screw into its lead screw nut from the top then insert them into the Z motor coupler by rotating them until fully seated

Tighten the upper screw of the coupler to hold the lead screw

Assembling the Z axis | 20


Place the Ender 3 Y plate onto the bed holders, followed by 4 silicone spacers (12mm version shown here in orange) or you may use the springs from the Ender 3, then the heatbed
Of course, the wiring of the heatbed should end towards the back of your printer


Use the original 4 M4x35 FHCS and secure them under the bed holders with M4 nuts

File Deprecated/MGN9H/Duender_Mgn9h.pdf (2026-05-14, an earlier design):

## Duender - MGN9H V-wheels Z axis

Your Open-Source 2 x Creality Ender-3 core XY conversion | by Sergei Irbis

## Some points of the build require your attention

## Linear rails handling

Once the printer is complete, the print bed and the nozzle will be heating and may cause severe burning if you are not cautious.
Do not touch those parts while in function.

A risk of overheating or electric short in components is always possible. In some cases, this could lead to the printer starting a fire.
Please, double check your build and babysit your printer during the tuning phase as well as its firsts jobs
Keeping an extinguisher near those appliances is a good practice.

Read the full doc before starting your build, and do not hesitate to reach out on the Discord server (https://discord.com/channels/1341676245171048473/1354698746524598312) to ask for help any time you are unsure

The rail axis carriages are meant to slide easily.

Be very careful they do not fall off the rail, as this would most likely result in irreparable damage.

When you receive them, they are very often covered in some kind of protective oil.
The video below by Canuck Creator offers all the advice you need to clean and lubricate your rails.

The MGN9H rails are quite thin and can be somewhat difficult to fit onto V-slut extrusions.
You can use some 3D printed helpers to align them: use spacers (https://www.printables.com/model/641406-v-slot-shim-adapters-mgn7-mgn9-positioning/files) or tools like this (https://www.printables.com/model/998923-2040-aluminum-extrusion-mgn9-alignment-tool) or this. (https://www.printables.com/model/450861-mgn9-mgn12-linear-rail-2020-alignment-tools)
Try tightening the screws progressively along the rail while maintaining alignment until all screws are secured.


https://2cm.es/1mI5J (https://youtu.be/UYvhYjkBFTY?si=c9C3WkopiexPDw9c)

# Table of contents

Hardware reference | 1
Bill of materials | 2
Important tips | 4
Extrusions reference | 6
Assembling the frame | 7
Z gantry | 16
AB gantry | 22
X axis gantry | 28
GT2 belts routing | 32
Power supply, control box and screen housings | 37
Wiring | 40
A few words about Medusa HC project | 47

https://2cm.es/1lYzA

https://2cm.es/1h2CE

https://2cm.es/1h2CJ

Need more information? | Wanna support the project? If you enjoy Duender and want to support what I do, there are a few ways to help: Patreon — monthly support https://patreon.com/Irbis3D Ko-fi / Buy Me a Coffee — one-time donations https://buymeacoffee.com/Irbis3D YouTube Super Thanks — under any video https://youtube.com/@Irbis3D Your support helps me create more content, upgrade gear, and keep experimenting with cool ideas. Thank you.

Sergei Irbis.

Know your bits | 1

## Hardware reference

SHCS (Socket Head Cap Screw)

Metric fastener with cylindrical head and hex drive

BHCS (Button Head Cap Screw)

Metric fastener with hemispheric head and hex drive. Mostly used with M5 T-slot nuts

T-slot nut

Nut that is inserted inside the slot of aluminium extrusions. Must be inserted on beforehand
Hammerhead T-nuts can be used after assembly

FHCS (Flat Head Cap Screw)

Metric fastener with cone shaped head and flat top

Hex nut

Coupled with a screw to create a bolt. Nylstop ones have a plastic insert to prevent them un-tightening

Heat-set insert

Once heated with the soldering iron, it melts into plastic, which makes a tight fit by solidifying.
M3 threading, 5 mm outer diam., 4 mm

Toothed idler

Has bearings inserted in the axis, used to redirect the belt in the motion system. GT2 refers to the belt pitch between teeth

Shim (or spacer)

Metal flat ring, with a set thickness, used as spacer between parts and bearings. Not to be confused with washers

Pin

Metal smooth rod but to size. Used as an axis for idlers.

Toothless idler

Similar idler without teeth, for the smooth side of the belt. 16T is for teeth count, 6W for belt width, 3B for axis bore diameter

BOM and sourcing | 2

## Bill of materials

Fasteners* | Qty | Order | Affiliated link / Notes | Hardware | Qty | Order | Affiliated link
M5x25 SHCS | 2 | ✓ | From Ender 3 | 42-34 Nema17 motor | 2 | ✓ | From Ender 3
M4x20 SHCS | 2 | ✓ | From Ender 3 | 42-40 Nema17 motor | 2 | ✓ | From Ender 3
M5x30 BHCS | 8 | ✓ | From Ender 3 | Leadscrew T8x8 mm 365 mm | 2 | ✓ | From Ender 3
M4x35 FHCS | 4 | ✓ | From Ender 3 | Eccentric column D7.2 d5 H8.35 mm | 4 | ✓ | From Ender 3
M5 hex locknut | 10 | ✓ | From Ender 3 | Spacer for rollers D8 d5 H8.35 mm | 4 | ✓ | From Ender 3
Corner bracket | 28 | | https://s.click.aliexpress.com/e/_c4DUW5sX | V-wheels rollers | 8 | ✓ | From Ender 3
M3x30 SHCS | 22 | | | Y plate | 1 | ✓ | From Ender 3
M3x20 SHCS | 2 | | https://s.click.aliexpress.com/e/_c2Rkq5Jx | Motor coupler D5x8 optional elastic coupler | 2 2 | ✓ | From Ender 3
M3x18 SHCS | 8
M3x16 SHCS | 6
M3x8 SHCS | 32 | | | 2020 V-slot 300mm extrusion | 1 | | If you install the front brace (see p.15)
M3x6 SHCS | 8 | | | MGN9H 300mm rail | 3 | | https://s.click.aliexpress.com/e/_oFYW0St
M5x8 BHCS | 94 | | | GT2 6mm wide belt | 5m | | https://s.click.aliexpress.com/e/_ooDLTEH
M5 T-slot nut | 79 | | https://s.click.aliexpress.com/e/_c4EDoXzD | Pulley GT2 16T 6W 5B | 2 | | https://s.click.aliexpress.com/e/_c4mjCdxl
M3 T-slot nut | 26 | | https://s.click.aliexpress.com/e/_c4EDoXzD | Toothed idler GT2 16T 6W 3B | 2 | | https://s.click.aliexpress.com/e/_c3Fqpe71
M4 hex locknut | 4 | | | Toothless Idler GT2 16T 6W 3B | 10 | | https://s.click.aliexpress.com/e/_c3Fqpe71
M3 hex nut | 20 | | | M3x0,5 mm shim | 48 | | https://s.click.aliexpress.com/e/_c4BNsuvz
M3 heat-set insert M3x5x4 | 28 | | https://s.click.aliexpress.com/e/_c4DbNkaX | M3x10 mm spacer | 1 | | https://s.click.aliexpress.com/e/_c3rUz3wF
Leadscrew brass nut Optional anti backlash nut | 2 2 | ✓ | From Ender 3

* Note that most of the time, SHCS can be replaced by BHCS and vice-versa. Please
check the manual to see where it may apply.

Long screws kit: https://s.click.aliexpress.com/e/_c4VYXcQR (colour: Button head) Short screws kit: https://s.click.aliexpress.com/e/_c30o44Xt

BOM and sourcing | 3

## If you are planning for Medusa HC:


Electronics | Qty | Order | Affiliated link

24V 15A PSU w/ housing, 10A switch, XT60 cable | 1 | ✓ | From Ender 3

Medusa HC is a toolhead changer specifically designed for
the Duender offering by default 4 swappable hotends.
If you use a board of your choice, with for example a
Raspberry Pi as your Klipper host, you may have to add a
second board to get enough hotend heaters and thermistors
ports available.
However, if you are considering using the BTT Manta 5P
recommended here, and planning for Medusa HC, it is
strongly advised to replace it right away with a BTT Manta 8P
with the CB2 board and the TMC2209 drivers so you can
expand and connect the hotends later on with no added
modification.

Heatbed 24V 235x235 mm | 1 | ✓ | From Ender 3

4010 24V axial fan | 2 | ✓ | From Ender 3

12864 screen w/ support plate Optional BTT HDMI5 V1.2 | 1 1 | ✓ | From Ender 3 https://s.click.aliexpress.com/e/_c4odBUeJ

BTT MANTA 5P | 1 | | https://s.click.aliexpress.com/e/_oktZaKt

BTT CB2 | 1 | | https://s.click.aliexpress.com/e/_oDMokmp

BTT TMC 2209 | 5 | | https://s.click.aliexpress.com/e/_oktZaKt

Misc | Qty | Order | Affiliated link

12 mm silicone bed spacer Optional Spring bed spacer Aluminium 60x66 mm 3 mm thick Optional Open build Plates | 4 4 2 2 | ✓ | From Ender 3

Voron Duender print settings:

Wires, connectors, pins, crimping pliers and stuff.

Material: ABS or ASA for all load-bearing parts
You can use a reinforced material (e.g. ABS-CF).
Electronics box and display holder may be printed
in any material
Layer height: 0.2 mm

Toolhead of choice | 1

Hotend of choice | 1

Extruder of choice | 1

No. of walls/top/bottom layers: 5 or 6

Infill: > 50% (60% recommended) for load bearing parts
Gyroid for strength, cross-hatch for speed.
Can be as low as 15% for electronics or screen
boxes

Last minute call | 4

## Important tips

## Ender 3 disassembly

DO NOT DISMANTLE THE POWER SUPPLY. You will use the PSU along with its cover, the power switch and the wire ending with an XT60 plug.

Deconstruction is easier if you first remove all connections from the mainboard; The connectors are held with hot glue, which you can carefully remove with a pair of pliers.

You can pull out the X axis after removing the top bar, which simplifies further deconstruction. The X motor has a QR code sticker, there are four screws underneath it.

You can easily remove the belts once you've loosened the belt tensioners.

The 4040 central profile and plastic parts won't be needed. Remove the rubber feet for easier squaring, but you may put them back later.

Depending on your batch, you may have to take the Ender 3 motors pulleys off. Some use a printed tool, (https://www.printables.com/model/230013-press-fit-pulley-extractor-for-nema-17) some just Dremel them out. Be careful!

## Z Axis

Alternatively to the 3 mm thick aluminium plate that needs to be cut and drilled for the Z axis plates, Openbuild plates can be used, they are more expensive at 2x€2.75, but have all the necessary holes. NOTE: you must use a remix of the bed carriages (https://www.printables.com/model/1302572-open-build-remix-for-duender-z-v2/collections) and adapt the screws (flat heads).

It is probably a good idea, to replace the Z motors shaft couplers with "spring motor coupler" ones at approx. 2x€2.50. In the same domain, it is advised to replace original brass lead screw nuts with anti-backlash spring loaded ones at approx. 2x€2.50 too.

## AB Axis

As this guide mentions, the original design suggests to cut one of the existing 2020 extrusions to size (top bar of the Ender 3) for the X axis, and considers an added top front brace to be "optional, but highly recommended ".
It is however recommended to buy a 300 mm 2020 extrusion for the X axis instead and use the second 330 mm 2020 extrusion for the front. This will add to the rigidity of the frame. Note that MedusaHC project will use a 350 mm 2020 extrusion here.

Toolhead (NOTE: because of Medusa HC, Dragonburner, with a Bambulab X1 series hotend and Sherpa mini extruder are the parts of choice.)
You can adapt many toolheads to the X rail carriage. Most popular choices include XOL, DragonBurner, and even original Ender 3 direct drive mods.

IMPORTANT NOTE: your choice may affect the heatbed positioning. You may need to unscrew lightly base and top Z rails axis M5x8 screws to slide the whole Z assembly front or back a few mm so your printhead travel can cover the whole size of the bed.

Last minute call | 5

## Electronics

While you can go with whatever board accepting Klipper, the BTT Manta M5P with a CB1/2 is likely the best choice but you can of course use a Raspberry Zero 2W and re-use the existing boards if you want to be really frugal. NOTE that flashing firmware on Creality boards can be tricky.

You may not need a display, as you’ll be able to use the web interface anyway, but the original 12864 of your Ender 3 can do the job, or you can get a proper Klipper compatible touch screen. Original design goes with a BTT TFT 35 SPI screen, but it’s not as responsive as you’d want.

Remember that you might need different hardware if you made different electronics choices.

## Building

During the frame assembly, it is critical that everything ends up square and flush.The base and four vertical posts should be placed first then squared while gradually tightening the frame. It is tedious but the print quality of your Duender depends on it.

Since MGN9H rails are about as wide as the V-slots, it's not easy to get them centred. You can print some spacers (https://www.printables.com/model/641406-v-slot-shim-adapters-mgn7-mgn9-positioning/files) or alignment tool like this (https://www.printables.com/model/998923-2040-aluminum-extrusion-mgn9-alignment-tool) or this. (https://www.printables.com/model/450861-mgn9-mgn12-linear-rail-2020-alignment-tools)

The belt tensioners are also quite fiddly since you need to get all washers and idlers lined up before putting the screw in. A printed jig (https://www.printables.com/model/1500832-duender-belt-tensioner-jig) may help you.

If you are unsure about how to correctly tap your extrusions, check out this video first:

https://2cm.es/1lYBi

Preparation | 6

## Extrusions reference

4 x 2040
400 mm long 2040-B Ender 3 Z axis

4 x 4040
290 mm long 4040-A Ender 3 feet | 2 x 2040 330 mm long
| Ender 3 Y axis

2040-C*

2 x 2020 345 mm long
Ender 3 x axis

2020-D *

2 x 2020 330 mm long
Ender 3 top bar

2020-E*

* Extrusions marked with an * need to be M5 tapped at both ends: 2040-C (8 channels), 2020-D (4 channels) and ONE of the 2020-E (2 channels).

Base structure | 7

## Assembling the frame


Metal corner bracket | 26 (28)
M5 T-slot nut | 69 (71)
M5x8 BHCS | 66 (70)

(Figures in brackets are with optional front brace)

Base structure | 8

Insert 2 M5 T-slot nuts in both the 2040-B (8 M5 T-slot nut total)

Make sure to orient the back 2040B extrusions so the mounting holes for the power supply are towards the inside of the printer (see picture on next page)

Place 2 brackets and
insert the M5x8 screws

Repeat at the other end
of each 4040-A

First, prepare each 4040-A with 11 M5 T-slot nut as shown here
You can keep the original Ender 3 plastic pads as feet on the underside (22 M5 T-slot nuts total)

Base structure | 9

Make sure everything is flush and square before final tightening

Once done, repeat the same steps with the remaining 4040-A and the two 2040-B to form the opposite side of the frame

Make sure the holes for the power supply end on the inside of the back 2040-B


Insert a M5 T-slot nut in the inside slot of each 2040-B post of the previous assemblies
(4 M5 T-slot nuts total)

Base structure | 10

Place the 4040-A flush and square to one side assembly and proceed installing the brackets with 6 M5x8 screws on each end (24 total)

Repeat those steps in the four corners of the base

Once done, double check all your alignments

It’s a good idea to measure each diagonal of the base square to make sure they are equal too!

Insert 6 M5 T-slot nut in each of the remaining 4040-A part as shown here (12 total)
Add the M5 T-slot nuts shown in picture in the relevant extrusions (15 total)

Front 4040-A only (screen housing)

Back 4040-A only (electronics box)

Base structure | 11

Carefully tap each end of the channel in both the 2020-D extrusions with an M5 bit

Install the Z motor mount onto one end of the extrusion, making sure it’s seated and flush, then secure it with a single M5x8 BHCS (2 M5x8 BHCS total)

as pictured (2 M5x8 BHCS total)

Do the same thing with the Z axis top spacer,

Base structure | 12

Install the Z axis onto one side of the base
Align the previously installed M5 T-slot nuts with the holes
Secure it with three M5x8 BHCS
(6 M5x8 BHCS total)

DO NOT FULLY TIGHTEN THE SCREWS YET The axis needs to be able to slide side to side

Use the 3D printed spacer provided in the tools
OR a calliper to adjust the Z axis 97 mm from the front post, then tighten the 3 M5x8 BHCS of the base

This is the default distance. You may need to adjust this distance later, depending on your toolhead configuration

Base structure | 13

Once done, insert 4 M5 T-slot nut on the underside of each one (8 M5 T-slot nuts total)


Insert an M5 T-slot nut on the top of each post, in the outside rail as shown (4 total) Place the 2040-C on top of each side

Make sure the extrusions are flush at each end then proceed and install the corner brackets (4 total)

Repeat those steps on the other side to assemble the second Z axis to the frame

Align the 2 M5 T-slot nuts remaining under the 2040-C with the top Z axis plate, and use 2 M5x8 BHCS to secure it

Check the distance to the front post to be

### 97 mm all along the Z axis before

tightening the screws

Check if channels of your 2040-C extrusions are already tapped.
If not carefully tap each one on each end of both extrusions with an M5 bit (8 channels total).

Base structure | 14

Carefully tap each end of the channel in the 2020-E extrusion with an M5 bit

Insert one M5 T-slot nut at the top of each rear Z posts
(2 M5 T-slot nut total)

For the rear right Z post only: add a second M5 T-slot nut (for the electronics box later on)

Align the 2020-E extrusion flush to the top of the Z posts The 2020-E must be centred between the posts Align the T-slot nuts
Install a corner bracket with 2 M5x8 BHCS
(4 M5x8 BHCS total)

Once done, insert 2 M5 T-slot nuts into the back rail, and 2 more into the front one

Base structure | 15


Chop off the last 2020-E extrusion to 300 mm long
and save it to assemble the X axis later on

You may prefer to buy a new 300 mm extrusion and keep the 330 mm 2020-E to make a front brace for rigidity purposes.
If that is your case, repeat steps on page 14 for the front part of the printer, and use your newly bought extrusion for the section starting on page 28

NOTE that if you are planning for MedusaHC mod later, the front brace needs to be 350 mm long. So best solution is to still cut 330 to 300 mm and buy a single 350 mm 2020 extrusion for the front brace.

Use a suitable metal cutting saw blade, Dremel bit or other adapted tool to make a clean cut

Assembling the Z axis | 16

## Z gantry

Lead screw nut | 2
(from Ender 3)
8 mm lead screw | 2
(from Ender 3)
Wheel M5 spacer | 4
(from Ender 3)
POM V-Wheel | 8
(from Ender 3)
M5 Nylstop nut | 8
(from Ender 3)
Eccentric M5 nut | 4
(from Ender 3)
M5x30 BHCS | 8
(from Ender 3)
Motor shaft coupler | 2
(from Ender 3)
M4x35 FHCS | 4
(from Ender 3)
M4 Nylstop nut | 4
DIY aluminum plates | 2
or Openbuild plates
M3x8 SHCS | 16
M3 Nylstop nut | 12
M3x16 SHCS | 4
12 mm silicone spacers | 4
Nema 17 42-34 | 2
(from Ender 3)

Assembling the Z axis | 17

You will need to prepare two plates in 3 mm thick aluminium. The STL templates will give you exact dimensions and holes sizes/locations.

If making those is a problem, a mod using Open build plates exists, with all the necessary holes pre-drilled.

Carefully tap the marked holes with a M3 threading bit

Assembling the Z axis | 18

Insert 4 M5x30 BHCS from the underside Spacers go over the smaller holes and

Install the lead screw nuts under the plastic bed holders, and insert 2 M3x16 SHCS or BHCS (Or you can use the ones originally coming from your Ender 3)

If your lead screws aren’t perfectly straight, it is advised that you swap the original lead screw nuts from the Ender 3 with some anti-backlash ones, to avoid Z wobble

eccentric nuts over the larger ones
Those are all from the original Ender 3 rollers mounts

Finally, add 4 V-rollers from your Ender 3, and

the wheel assemblies loose for adjustment


Turn the bed holders around being careful not to lose the screws and secure them with M3 nuts

Assembling the Z axis | 19

Place the rollers plate behind the bed holder and use 4 M3x8 SHCS to secure it The screws should bite directly into the threads in the aluminium plate.
Alternatively, you may use M3x12 SHCS and secure them with 4 M3 hex nuts from the back of the plate, as pictured.

Remember that if you used open builds plates, screws will go back to front, and you’ll want to double check for their head not touching the Z extrusion.

Place the Z motors under their plates and use 4 M3x8 SHCS to secure them. Orient the motor plug to the back of the printer


Install the lead screws couplers onto the Z motors shafts and tighten only the lower screw

If your lead screws aren’t perfectly straight, you may want to replace those with "spring" or "elastic" ones to avoid Z-wobble

Assembling the Z axis | 20

Insert the bed holder assembly onto the Z axis (note that the longer side goes towards the front) and tighten the V-wheels
Once secured, adjust the eccentric nuts to ensure all 4 wheels apply equal pressure

The wheels should rotate smoothly with a slight resistance when turned by hand

Double-check that the screw heads don’t touch the extrusion surface.


Insert each lead screw into its lead screw nut from the top then insert them into the Z motor coupler by rotating them until fully seated

Tighten the upper screw of the coupler to hold the lead screw

Assembling the Z axis | 21

Place the Ender 3 Y plate onto the bed holders, followed by 4 silicone spacers (12 mm version shown here in orange) or you may use the springs from the Ender 3, then the heatbed
Of course, the wiring of the heatbed should end towards the back of your printer


Use the original 4 M4x35 FHCS and secure them under the bed holders with M4 nuts

Building the AB kinematics | 22

## AB gantry

M5 T-slot nut | 2
M3 heat-set insert | 10
M3x0.5 spacer | 28
M5x8 BHCS | 14
M3x10 spacer | 1
Nema 17 42-40 | 2
(from Ender 3)

GT2 16T6W3B toothless idler 8

GT2 16T6W5B motor pulley 2

M5 Nylstop nut | 2
(from Ender 3)
M3x30 SHCS | 12 | MGN9H 300 mm rail | 2
M3x8 SHCS | 22
M3 T-slot nut | 18
M3x16 SHCS | 2
M3x20 SHCS | 2

Building the AB kinematics | 23

Prepare the bottom part of AB motor holders: with 6 M3 heat-set inserts each side
(12 M3 heat-set inserts total).

Install the motors under the plates with 2 M3x8 SHCS in the shown locations
Mind the motor plug orientation

Also place the motor pulleys onto the shafts of A & B motors
Do not tighten them too much. They will need to be adjusted later, after belts installation

Pass 2 M3x30 SHCS into the idler holes and turn both top halves upside down.


For the Left AB mount:

On the innermost pin (right side when upside down), stack:
- 2 M3x0.5 mm spacers,
- 1 GT2 16T toothless idler,
- 2 M3x0.5 mm spacers,
- 1 GT2 16T toothless idler,
- 2 M3x0.5 mm spacers.
- On the innermost pin, stack: 2 M3x0.5 mm spacers,
- 1 GT2 16T toothless idler,
- 2 M3x0.5 mm spacers,
- 1 M3x10 mm spacer.

The best option is certainly to buy and install a metal M3x10 spacer, but should you not have one on hand, you may use the printed one provided in the stl files.

Building the AB kinematics | 24

When the mounts are placed against each other, the idlers should be perfectly level between both sides. If that is not the case, adjust the spacer count as needed.

Install 9 M3 T-slot nuts then 1 M5 T-slot nut on top of each Y axis.
If you have hammerhead nuts on hand, it’s better to insert only 8 M3 T-slot nuts.

For the Right AB mount:

Onto the outermost pin (left side when upside down), stack:
- 2 M3x0.5 mm spacers,
- 1 GT2 16T toothless idler,
- 2 M3x0.5 mm spacers,
- 1 GT2 16T toothless idler,
- 2 M3x0.5 mm spacers.

Onto the innermost printed post pin:
- 3 M3x0.5 mm spacers,
- 1 GT2 16T toothless idler,
- 2 M3x0.5 mm spacers.


Lay the assembly on its back to prevent the spacers from falling out and assemble the two halves together.
Secure the assembly with 4 M3x30 SHCS on each side.
(12 M3x30 SHCS total)

Building the AB kinematics | 25

Install the AB motor holders on each side and use a M5x8 BHCS to secure it onto the top M5 T-slot nut

Use a second M5x8 BHCS threaded into the tapped end of the 2020-E back brace

Use a M5x8 BHCS threaded into the tapped end of the 2040-C Y axis and another one into the back brace M5 T-slot nut

Building the AB kinematics | 26


Install the motor holders with M3x16 SHCS threaded directly into the motor

Secure the base of the holder with an M5x8 BHCS into one of the previously inserted T-slot nuts in front of the back brace

Install the MGN9H rails against the motor holders with the help of 3D printed centring jig and 8 M3x8 SHCS

DO NOT FULLY TIGHTEN THE SCREWS YET


Install the Y carriage stopper with 1 M3x8 SHCS onto the last M3 T-slot nut.

If you have hammerhead nuts, use 2 of them to install the stopper, as it may help you to replace it with another accessory later.

Building the AB kinematics | 27

Install the front holders with 2 M5x8 BHCS on each side

Mind the side, the holders are not symmetrical

Prepare both the Left and Right belt tensioners by placing an M3 heat-set insert in the underside hole

Place
- 2 M3x0.5 mm spacers,
- 1 GT2 16T toothless idler,
- 2 M3x0.5 mm spacers,
all held by a M3x20 SHCS inside each tensioner

As already mentioned, a printed jig (https://www.printables.com/model/1500832-duender-belt-tensioner-jig) can make this much easier

Insert an M5 Nylstop nut into the groove inside both holders. A light dab of glue may be used to ensure they stay in place.

Building the X axis | 28

## X axis gantry

M3x30 SHCS; M3x8 SHCS; M5 T-slot nut; M5x8 BHCS; M3 T-slot nut; M3 heat-set insert; M3x0.5 spacer; M3x6 SHCS

MGN9H 300 mm rail | 1

GT2 16T6W3B toothless idler 2

GT2 16T6W3B toothed idler 2

Building the X axis | 29

Prepare both bottom parts of the X carriage with 5 M3 heat-set inserts each side.
The inserts in the printed posts are easier to install from below.

Each half takes:
Onto the frontmost axis
- 2 M3x0.5 mm spacers,
- 1 GT2 16T toothed idler,
- 3 M3x0.5 mm spacers.

Onto the rearmost axis:
- 2 M3x0.5 mm spacers,
- 1 GT2 16T toothless idler
- 3 M3x0.5 mm spacers.
Turn both top halves upside down, and insert 2 M3x30 SHCS each side to serve as the idler axis

Attach both bottom halves onto their rail carriage using 4 M3x6 SHCS
(8 M3x6 SHCS total).

Building the X axis | 30

Lay the printer on its back to prevent the spacers from falling out and tighten both sides of the X axis assembly, adding 3 M3x30 SHCS, to assemble the two halves.
( 6 M3x30 SHCS total)

Just screw enough so that parts hold together: both halves need to be loose for the next step.

Assemble the 8 M3 T-slot nuts to the last 300 mm rail with 8 M3x8 SHCS. Leave them loose enough to slide into the 300 mm X axis extrusion.
Center the rail flush both sides and, using a centring jig, tighten the screws to secure the assembly.
(8 M3 T-slot nuts and 8 M3x8 SHCS total)

Insert 2 M5 T-slot nuts on the top side, 2

axis extrusion
(6 M5 T-slot nuts total)

Push the X axis into its carriages on the two sides of the printer, carefully centre it, then tighten both carriages.

Once done, use the previously inserted T-nuts to tighten 3 M5x8 BHCS at each end:
1 on top, 1 on the back and 1 under the X axis.
(6 M5x8 BHCS total)

Building the X axis | 31

Finally, slide the X axis assembly back and forth several times to allow the Y rails to self-align. Gradually tighten the M3x8 screws each side from one end to another to lock the rails in place.

(Note that the toolhead carriage will be attached to the rail with 4 M3x6 SHCS shown here.)

A & B belts installation | 32

## GT2 belts routing


"Equal belt tension is important to the proper function of a CoreXY motion system.

We recommend to run one belt to get the required length, remove the belt from the printer and cut the second belt to the exact same length.

As both belt paths have the same length this is an easy way of getting a consistent tension."

- The Voron team

GT2 6 mm belt approx. 2x1,5m

M5x25 SHCS | 2
(from Ender 3)

A & B belts installation | 33

## A belt

Pass the belt into the L side tensioner (flat side against idler) then insert the tensioner into the L front holder, and secure it with a M5x25 SHCS passing from the front of the holder

Pass the short side of the belt into the toothed idler and towards the X axis toolhead carriage

The longer side passes next to the left Y carriage all the way to the AB motor holder at the back left
Use the lower idler to turn 90° and head to the right AB motor holder

A & B belts installation | 34


1: Into the right AB motor holder, use the first idler to redirect the belt towards the motor pulley (not shown here)
2: Place the belt into the A motor pulley, it’s time to adjust pulley height. Then back to the second idler (the lower one) to
3: continue towards the front of the printer

Finally, use the lower idler inside the right Y axis carriage to turn 90° and head to the right side of the printhead carriage

You will need to use whichever toolhead carriage you have chosen to hold both extremities of the belt

As an example, here are both sides of the belt inserted in a Dragonburner MGN9H carriage

Once secured, cut the belt to the correct length, and unmount it to use as reference

Place the freshly cut A belt on top of the remaining GT2 length and make sure they stay perfectly flush (you can tape them together) Cut the second belt at the exact dimension, the same teeth count now means the same tension later

You can now reinstall the A belt with the same exact procedure you just followed

A & B belts installation | 35

## B belt


Pass the belt into the R side tensioner (flat side against idler) then insert the tensioner into the R front holder, and secure it with a M5x25 SHCS passing from the front hole of the holder

Pass the short side of the belt into the toothed idler and towards the X axis toolhead carriage

The longer side passes next to the right Y carriage all the way to the AB motor holder at the back right
Use the upper idler to turn 90° and head to the left AB motor holder

A & B belts installation | 36

As an example, here are both belts inserted in a Dragonburner MGN9H carriage, ready to roll

IMPORTANT: Double check that both belts are perfectly level and straight all along their path

If that is not the case, you may need to adjust the number of M3x0.5 mm spacers used to level the idlers

Also check for the A and B motors pulleys height. You may have to unscrew them a bit to align them with the belts
It may be a good idea to add a drop of threadlocker to the grub screws of the pulleys before final tightening

Finally, use the upper idler inside the left Y axis carriage to turn 90° and head to the left side of the printhead carriage

You will need to use whichever toolhead carriage you have chosen to hold both extremities of the belt

1: Into the left AB motor holder, use the first idler to redirect the belt towards the motor pulley (not shown here)
2: Place the belt into the B motor pulley, it’s time to adjust pulley height. Then back to the second idler (the upper one)
3: continue towards the front of the printer

PSU, control box & screen | 37

## Power supply, control box and screen housings

M5x8 BHCS; M3 heat-set insert; M4x20 SHCS; (from Ender 3); 12864 display assembly; 24V 15A PSU

PSU, control box & screen | 38

Prepare the bottom of the electronics box by inserting 8 heat-set inserts, one into each corner hole, and on the inside mainboard pillars

Use original M4x20 SHCS to attach the original power supply to the back left 2040-B Z post

Place the electronics box in the back lower right corner of the frame, and use the two remaining M5 T-slot nuts to secure it with 2 M5x8 BHCS

Box shown is for BTT Manta 5P mainboard. You may need other model depending on your choices

PSU, control box & screen | 39

You may use the original Ender 3 12864 screen

It can be mounted to the front of your Duender using the last two remaining M5 T-slot nuts with M5x8 BHCS

The original Duender build however is made with a BTT TFT 35 SPI screen
It can be mounted to the front of your Duender using the last two remaining M5 T-slot nuts with M5x8 BHCS
THIS SOLUTION IS NOT RECOMMENDED, as this touch screen seems sluggish. You can replace it with any Klipper compatible screen. Keep in mind that by doing so you will need a specific screen housing

Mainboard installation | 40

## Wiring

This section is intended for the BTT Manta 5P mainboard loaded with a CB1/CB2

You will find all the information you need on the BTT Wiki: https://2cm.es/1lYBC (https://global.bttwiki.com/M5P.html)
Files and firmware can be downloaded from the GitHub: https://2cm.es/1h2DL (https://github.com/bigtreetech/Manta-M5P/)

Keep in mind you may need to extend or completely remake some cables, and for this some tools like a soldering iron, good crimping pliers and a set of connectors will prove more than useful

Reference image from Victor Bared’s Manta 5P video series. Jumpers setup, image install: https://2cm.es/1lYBp (https://youtu.be/Mec3cZnCP18?si=VkWnbPqD_my4Xc08) Wiring: https://2cm.es/1lYBr (https://youtu.be/LZFxCJQfl8I?si=Z7Ys0Ox6w-WK8Ww8)

BTT Manta M5P | 1
or M8P for Medusa
BTT CB1 OR CB2 | 1
TMC2209 driver | 5
Micro-JST connectors | some
and pins

Wires in different colours plenty 1 mm², 0.5 mm² etc.

M3x8 SHCS | 8
M3x18 SHCS | 8
M3 Nylstop nut | 8
4010 axial fan | 2
(from Ender 3)

Mainboard installation | 41

## Jumpers basics


TMC2209 UART mode

VBB

VBB

VBB

VBB

VBB

24V motors power

24V 12V 5V

Fan0
Parts cooling fan

Fan1
Hotend fan

Fan
Electronics fan

Fans voltage choices

Wifi antenna plug

Mainboard installation | 42

## Toolhead and heatbed wires

(TB)

Heatbed thermistor

Heatbed heater
(HB)

Parts cooling fans
(Fan0)

Extruder motor
(Motor 5)

Hotend fan
(Fan1)

Hotend thermistor
(TH0)

Heating cartridge
(HE0)

As an example, a Dragonburner toolhead with a Galileo2 extruder and a E3D Voron hotend
However, any toolhead configuration should have the same connectors to the mainboard

Mainboard installation | 43

## Mainboard ports

drivers sockets; Parts cooling fan; Same as Z0 (not used); (Fan0); Hotend fan (Fan1); Electronics case fan (Fan)

Green wiring goes to hotend Blue wiring goes to heatbed

XT60 cable from Ender 3
24 V DC from power supply

Heating Bed (HB)
No polarity

Bed Thermistor (TB)
No polarity

TMC2209 x 5

Hotend Thermistor (TH0)
No polarity

Hotend heating cartridge (HE0) No polarity

B motor plug (left hand)

A motor plug (right hand)

Z0 motor plug (right hand)

Z1 motor plug (left hand)

Extruder motor plug

Mainboard installation | 44

## Going home

You should now be ready to insert your Manta 5P into the electronics control box
Secure it with 4 M3x8 SHCS, and go ahead with all your connections

Make good use of all the box cutouts to manage your cables and secure them with zipties or other sleeving of your choice

Temporary jumper to power the board by USB

To flash the image onto the CB1 microSD card, you may need to use the shown jumper and power the mainboard with 5V by USB cable

Mainboard installation | 45

## (Nearly) Everything you ever wanted to know about Klipper

https://2cm.es/1i1XM (https://www.youtube.com/watch?v=JQFw9zdHB5w) | https://2cm.es/1n0Wo (https://www.youtube.com/watch?v=-e81KhcYGCA)
https://2cm.es/1n0Yt (https://www.youtube.com/watch?v=bj69-lfF6FQ) | https://2cm.es/1i1Yq (https://www.youtube.com/watch?v=mIDtFIi-M4w)

Mainboard installation | 46

## Electronics case fans


Congratulations! Your build is now complete! Next step is installing Klipper and building your printer.cfg file Once your printer is alive, we can only recommend the excellent Ellis’ Print Tuning Guide: https://ellis3dp.com/Print-Tuning-Guide/

## We wish you loads of prints and fun with your Duender!

Once you are all done, use the last 4 M3x8 SHCS to close the electronics box

You may want to cool down your electronics with two 4010 axial fans taken from the E3 toolheads

You can use 8 M3x18 SHCS with 8 M3 nuts to secure them to the box lid

Electronics fans
(Fan)

+

Coming soon! | 47

## A few words about Medusa HC project

https://youtu.be/hpV5Z1TnGdY?si=FyJBHvE2mylvz7cY or https://2cm.es/1mI62

What? You want more?
Ok… What if I told you that your Duender can have up to 4 different toolheads? What if you could print 4 different colours or even 4 different materials at the same time, without needing to poop-purge?

Sounds great, doesn’t it? Well stay tuned, because your open-source, budget multi-toolhead mod for the Duender is coming to you.

More info on Irbis 3D channel : https://2cm.es/1h7sX

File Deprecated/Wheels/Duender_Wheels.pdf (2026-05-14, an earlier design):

Your Open-Source 2 x Creality Ender-3 core XY conversion | by Sergei Irbis ADDON ⁻ “Mgn9h” version”

## Duender V-wheels AB & X axis

Building the AB kinematics | 22

## AB Gantry

M3x0.5 spacer; Nema 17 42-40; (from Ender 3); M3x30 SHCS; M3x8 SHCS; M3x16 SHCS; M3x20 SHCS
M5 T-slot nut; M3 Heat set insert; M3x10 spacer; M5x8 BHCS screw; GT2 16T6W3B toothless idler 8; GT2 16T6W5B motor pulley 2; M5 Nylstop nut; (from Ender 3); Wheel M5 spacer; POM V-Wheel; Eccentric M5 nut; M5x30 BHCS screw

Building the AB kinematics | 23


Prepare the bottom part of AB motor holders: with 6 M3 heat-set inserts each side
(12 M3 heat-set inserts total).

Install the motors under the plates with 2 M3x8 SHCS screws in the shown locations Mind the motor plug orientation

Also place the motor pulleys onto the shafts of A & B motors
Do not tighten them too much. They will need to be adjusted later, after belts installation


Pass 2 M3x30 SHCS into the idler holes and turn both top halves upside down.


For the Left AB mount:

Onto the outermost pin (right side when upside down), stack:
- 2 M3x0.5 mm spacers,
- 1 GT2 16T toothless idler,
- 2 M3x0.5 mm spacers,
- 1 GT2 16T toothless idler,
- 2 M3x0.5 mm spacers

On the innermost pin:
- 2 M3x0.5 mm spacers,
- 1 GT2 16T toothless idler,
- 2 more M3x0.5 mm spacers,
- 1 M3x10 mm spacer

The best option is certainly to buy and install a metal M3x10 spacer, but should you not have one on hand, you may use the printed one provided in the stl files.

Building the AB kinematics | 24


When the mounts are placed against each other, the idlers should be perfectly level between both sides. If that is not the case, adjust the spacer count as needed.

For the Right AB mount:

Onto the outermost pin (left side when upside down), stack:
- 2 M3x0.5 mm spacers,
- 1 GT2 16T toothless idler,
- 2 M3x0.5 mm spacers,
- 1 GT2 16T toothless idler,
- 2 M3x0.5 mm spacers.

Onto the innermost printed post pin:
- 3 M3x0.5 mm spacers,
- 1 GT2 16T toothless idler,
- 2 M3x0.5 mm spacers.


Lay the assembly on its back to prevent the spacers from falling out and assemble the two halves together.
Secure them adding 4 M3x30 SHCS on each side. (12 M3x30 SHCS total)

Building the AB kinematics | 25


Install the AB motor holders on each side and use a M5x8 BHCS screw to secure it onto the top M5 T-slot nut


Use a second M5x8 BHCS secured into the tapped end of the 2020-E back brace

Use a M5x8 BHCS to hold into the tapped end of the 2040-C Y axis and another one to hold onto the back brace M5 T-slot nut

Building the AB kinematics | 26


Install the motor holders with M3x16 SHCS threaded into the motor

Secure the base of the holder with an M5x8 BHCS screw into one of the previously inserted T-slot nuts in front of the back brace


Prepare both carriage plates by inserting 4 M3 heat-set inserts each side
(8 M3 heat inserts total).

Just like the Z plates, insert 3 M5x30 BHCS into each carriage, then on the outer side, each takes:
- 1 M5 spacer,
- 1 V-wheel,
- 1 M5 hex nut.
On the inner side, stack:
- 1 eccentric nut,
- 1 V-wheel,
- 1 M5 hex nut to tighten the whole.
Leave them loose for now.

(6 M5x30 BHCS, 4 M5 spacers, 2 eccentric columns, 6 V-wheels and 6 M5 hex nuts total)


Place the carriages on both Y axis rails and tighten the M5 hex nuts, then adjust the eccentric nuts to set the carriage preload.

Building the AB kinematics | 27

Install the front holders with 2 M5x8 BHCS on each side

Mind the side, the holders are not symmetrical


Prepare both the left and right belt tensioners by placing an M3 heat-set insert in the underside hole


Place
- 2 M3x0.5 mm spacers,
- 1 16T toothless idler,
- 2 M3x0.5 mm spacers,
all held by a M3x20 SHCS screw inside each tensioner

As already mentioned, a printed jig (https://www.printables.com/model/1500832-duender-belt-tensioner-jig) can make this much easier

Insert an M5 Nylstop nut into the groove inside both holders. A small dab of glue may be used to keep them in place.

Building the X axis | 28

## X axis gantry

M3x30 SHCS; M5 T-slot nut; M5x8 BHCS screw; M3 Heat set insert; M3x0.5 spacer; GT216T6W3B toothless idler 2; GT2 16T6W3B toothed idler 2; M3x6 SHCS; Modified toolhead plate; (from Ender 3)
Wheel M5 spacer; (from Ender 3); POM V-Wheel; Eccentric M5 nut; M5x30 BHCS screw; M5 Nylstop nut

Building the X axis | 29


Each half takes:
On the front axis
- 2 M3x0.5 mm spacers,
- 1 GT2 16T toothed idler,
- 3 M3x0.5 mm spacers

On the rear axis
- 2 M3x0.5 mm spacers,
- 1 GT2 16T toothless idler,
- 3 M3x0.5 mm spacers.

Turn both top halves upside down, and insert 2 M3x30 SHCS each side to serve as the idler axis

Prepare both bottom parts of the X carriage with 5 M3 heat-set inserts on each side.
Those in the printed posts are easier to insert from below.

Place each bottom half onto its carriage, and secure it with 4 M3x6 SHCS
(8 M3x6 SHCS total).

Building the X axis | 30

on the back side and 2 more under the X

Insert 2 M5 T-slot nuts on the top side, 2

axis extrusion
(6 M5 T-slot nuts total)

assemble the two halves. ( 6 M3x30 SHCS total); Just screw enough so that parts hold together: both halves need to be loose for the next step.

Push the X axis into its carriages on the two sides of the printer, carefully centre it, then tighten both carriages.

Once done, use the previously inserted T-nuts to tighten 3 M5x8 BHCS at each end:
1 on top, 1 on the back and 1 under the X axis.
(6 M5x8 BHCS total)

Lay the printer on its back to prevent the spacers from falling out and tighten both sides of the X-axis assembly, adding 3 M3x30 SHCS, to

Place a M5x30 BHCS into the bottom of the toolhead plate, from below, stack:
- 1 eccentric nut,
- 1 V-wheel,
- 1 M5 hex nut.
Leave the nut loose for now.

Onto each M5x30 BHCS through the top of the plate, stack:
1 wheel spacer,
1 V-wheel,
1 M5 hex nut.
Leave the nut loose for now.

Building the X axis | 31


Put the adapter plate onto the metal carriage, and attach it using 2 M5x30 BHCS that hold a M5 spacer, a V-wheel and a M5 hex nut from below.
Leave the nuts loose for now.

Position the wheels onto the X extrusion, the belts (installed in next section) will pass through the side openings, be folded onto themselves behind the metal plate secured with a zip tie.

Once aligned, tighten the M5 nuts to secure the wheel assembly onto the extrusion, then adjust the eccentric nut to set the carriage preload.


Once assembled, the toolhead will be attached to the carriage using 2 M3x8 SHCS on the bottom, and 1 M3x18 SHCS on the top.

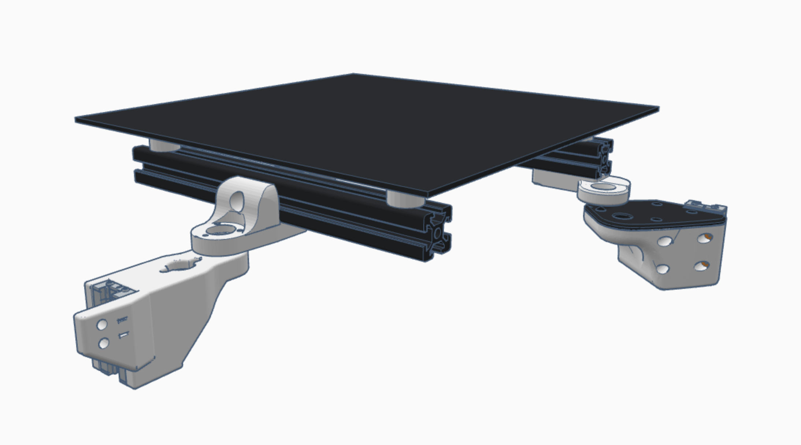
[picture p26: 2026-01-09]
Kinematic 3Z - in progress/screenshot_back.png

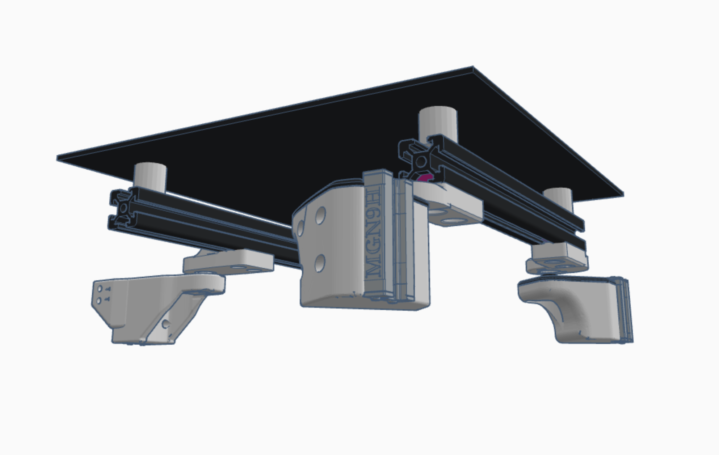
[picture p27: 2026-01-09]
Kinematic 3Z - in progress/screenshot_front.png

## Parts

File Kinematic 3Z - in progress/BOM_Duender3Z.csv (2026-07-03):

Item | Quantity | Description | Product line
1 | 1 | Base_Cover | DIY Acrylic panel
2 | 2 | 4040-A 290mm extrusion | Ender 3 part
3 | 2 | 4040-A 290m extrusion | Ender 3 part
4 | 4 | 2040-B 400mm extrusion | Ender 3 part
5 | 2 | 2040-C 345mm extrusion | Ender 3 part
6 | 2 | 2020-E 345mm extrusion | Ender 3 part
7 | 5 | Nema 17 42-34 motor | Ender 3 part
8 | 3 | Motor coupler D5/8 | Ender 3 part
9 | 3 | T8 lead screw | Ender 3 part
10 | 1 | 235x235 Heat bed | Ender 3 part
11 | 2 | M5x25 SHCS | Ender 3 part
12 | 1 | 2040-C 345mm extrusion | Extrusion
13 | 1 | 2020-E 345mm extrusion | Extrusion
14 | 2 | 2020V 200mm | Extrusion
15 | 1 | 2020V 300mm | Extrusion
16 | 1 | 2020 Vslot 350mm | Extrusion
17 | 107 | M5x8 BHCS | Fastener
18 | 47 | M5 T-slot Nut | Fastener
19 | 3 | M5x16 BHCS | Fastener
20 | 3 | M5x5x7 Heat set insert | Fastener
21 | 4 | M4x25 FHCS | Fastener
22 | 95 | M3x8 SHCS | Fastener
23 | 24 | M3x6 SHCS | Fastener
24 | 11 | M3x6 BHCS | Fastener
25 | 67 | M3 T-slot nut | Fastener
26 | 120 | M3x4.5x4 Heat-set insert | Fastener
27 | 27 | M3 Hex nut | Fastener
28 | 3 | TR8x8 leadscrew nut | Fastener
29 | 3 | GE5C bearing | Fastener
30 | 2 | M5 Hex nut | Fastener
31 | 52 | M3x8 BHCS | Fastener
32 | 2 | M3 Hammerhead T-nut | Fastener
33 | 6 | M3x35 SHCS | Fastener
34 | 14 | M3x30 SHCS | Fastener
35 | 24 | M2x10 BHCS | Fastener
36 | 16 | M2x3x4 Heatset Insert | Fastener
37 | 8 | M5x45 SCHS (from Ender) | Fastener
38 | 2 | M4 Hex nut | Fastener
39 | 16 | M3x18 BHCS | Fastener
40 | 4 | M5 T-slot nut | Fastener
41 | 30 | M3x10 BHCS | Fastener
42 | 10 | M3x14 BHCS | Fastener
43 | 3 | M3x20 BHCS | Fastener
44 | 5 | M3x12 BHCS | Fastener
45 | 1 | M3x45 BHCS | Fastener
46 | 2 | M3x30 BHCS | Fastener
47 | 3 | M3x4 set screw | Fastener
48 | 1 | M3x25 BHCS | Fastener
49 | 4 | 12mm silicone spacer | Hardware
50 | 12 | M3x30 pin | Hardware
51 | 5 | M3x20 pin | Hardware
52 | 7 | Limit switch | Hardware
53 | 42 | Neodym magnet 5x2mm | Hardware
54 | 4 | PTFE tubing 17mm | Hardware
55 | 5 | Neodym Magnet 12x3 | Hardware
56 | 4 | 3010 Axial Fan | Hardware
57 | 4 | Bambulab P1P Nozzle | Hardware
58 | 4 | Bambulab P1P Heatsink | Hardware
59 | 8 | 3.1x5x18 Aluminium Bushing | Hardware
60 | 8 | 3.1x5x25 Aluminium Bushing | Hardware
61 | 1 | Eddy V1 | Hardware
62 | 2 | 4010 Radial Fan | Hardware
63 | 1 | M3x6 pin | Hardware
64 | 1 | MG90S Servo | Hardware
65 | 2 | Sherpa 50t gear | Hardware
66 | 4 | Sherpa MR85-2RS | Hardware
67 | 2 | Sherpa 5mm shaft | Hardware
68 | 1 | Sherpa Nema14 10t | Hardware
69 | 1 | Sherpa filament gear | Hardware
70 | 1 | F693-2RS bearing | Hardware
71 | 1 | Sherpa Idler gear | Hardware
72 | 2 | Sherpa Needle bearings | Hardware
73 | 2 | Sherpa Spring | Hardware
74 | 2 | Sherpa Thumbscrew | Hardware
75 | 6 | MGN9H 300mm rail | Kinematics
76 | 6 | MGN9H carriage | Kinematics
77 | 39 | M3x0.5mm shim | Kinematics
78 | 5 | M3x10mm spacer | Kinematics
79 | 10 | 16T 6W 3B toothless idler | Kinematics
80 | 2 | GT2 16T 6W 5B pulley | Kinematics
81 | 2 | F695-2RS bearing | Kinematics
82 | 1 | GT2 6mm belt approx. 1.5m | Kinematics
83 | 1 | GT2 6mm belt approx. 1.5m | Kinematics
84 | 2 | 16T6W3B toothed idler | Kinematics
85 | 3 | Top Z spacer | Printed part
86 | 2 | Bottom Z spacer | Printed part
87 | 1 | Z motor holder back | Printed part
88 | 6 | Z Carriage stopper | Printed part
89 | 1 | Z joint back | Printed part
90 | 1 | Z motor holder front | Printed part
91 | 1 | Left joint | Printed Part
92 | 1 | Left joint cover | Printed Part
93 | 1 | Z_Motor_Plate_Right | Printed Part
94 | 1 | Right joint | Printed Part
95 | 1 | Right joint cover | Printed Part
96 | 1 | Bed support back | Printed part
97 | 1 | Bed support left | Printed part
98 | 1 | Z Right Bed Holder | Printed Part
99 | 1 | AB motor mount BottomLeft | Printed part
100 | 1 | AB motor mount TopLeft | Printed part
101 | 2 | Y Carriage stopper | Printed part
102 | 1 | Left Tensioner Bottom | Printed part
103 | 1 | Left Tensioner Top | Printed part
104 | 1 | AB motor mount BottomRight | Printed part
105 | 1 | AB motor mount TopRight | Printed part
106 | 1 | Right Tensioner Bottom | Printed part
107 | 1 | Right Tensioner Top | Printed part
108 | 1 | Y Carriage Bottom Left | Printed part
109 | 1 | Y Carriage Bottom Right | Printed part
110 | 1 | Y Carriage Top Left | Printed part
111 | 1 | Y Carriage Top Right | Printed part
112 | 2 | FL-BR_Leg_x2 | Printed Part
113 | 2 | Side_Skirt_x2 | Printed Part
114 | 2 | FR-BL_Leg_x2 | Printed Part
115 | 1 | Back_Skirt | Printed Part
116 | 1 | Plug_Plate | Printed Part
117 | 4 | 5010fan_Dummy_x4 | Printed Part
118 | 1 | Front_Skirt | Printed Part
119 | 2 | MicroUSB_Insert | Printed Part
120 | 4 | 5010fan_Grill_x4 | Printed Part
121 | 1 | EMS_Grill | Printed Part
122 | 1 | FT-EMS_Foot | Printed Part
123 | 1 | MHC Mount Left | Printed Part
124 | 1 | MHC Mount Right | Printed Part
125 | 4 | Base_Bin | Printed Part
126 | 4 | Base_Bin_Main | Printed Part
127 | 4 | Base_Mount_Plate | Printed Part
128 | 4 | Base_Mount_Main | Printed Part
129 | 4 | Nozzle_Close | Printed Part
130 | 4 | Brush_Mount | Printed Part
131 | 4 | Hotend_Mirrored_Bushings_x4 | Printed Part
132 | 1 | MGN9H_Mount_Cutout | Printed Part
133 | 1 | MGN9H_Mount_Eddy | Printed Part
134 | 1 | Extruder_Main | Printed Part
135 | 1 | Feeder_Body_1 | Printed Part
136 | 1 | Feeder_Lever_2 | Printed Part
137 | 1 | M90S_Opener | Printed Part
138 | 1 | Feeder_Lever_2 | Printed Part
139 | 1 | Servo_Mount | Printed Part
140 | 1 | Feeder_Body_2 | Printed Part
141 | 1 | Feeder_Opener | Printed Part
142 | 1 | Feeder_Lever_Main | Printed Part
143 | 1 | Feeder_Small_Cover | Printed Part
144 | 1 | HDMI5_Base | Printed Part
145 | 1 | HDMI5_Support | Printed Part
146 | 1 | HDMI5_Frame | Printed Part

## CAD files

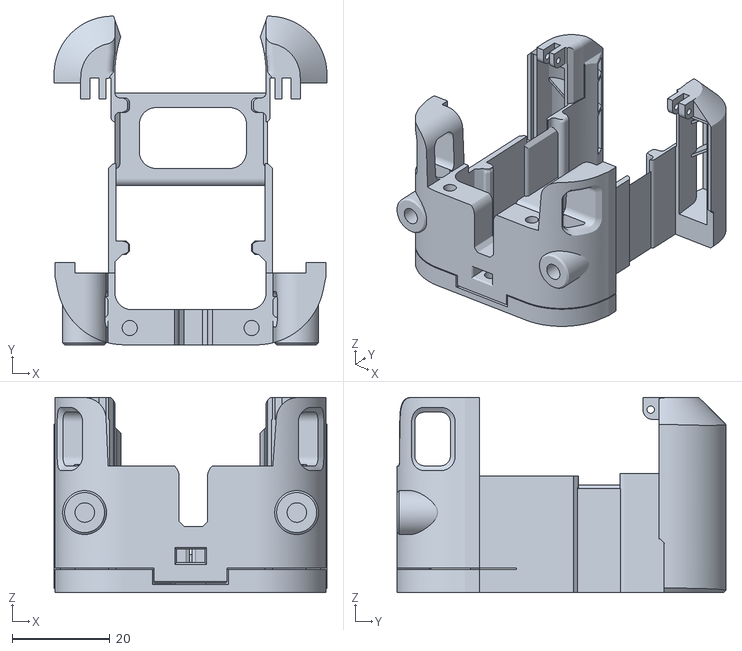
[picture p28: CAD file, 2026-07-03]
Kinematic 3Z - in progress/Toolhead/Toolhead_Extruder_Main.stl
56.0 x 67.4 x 40.0

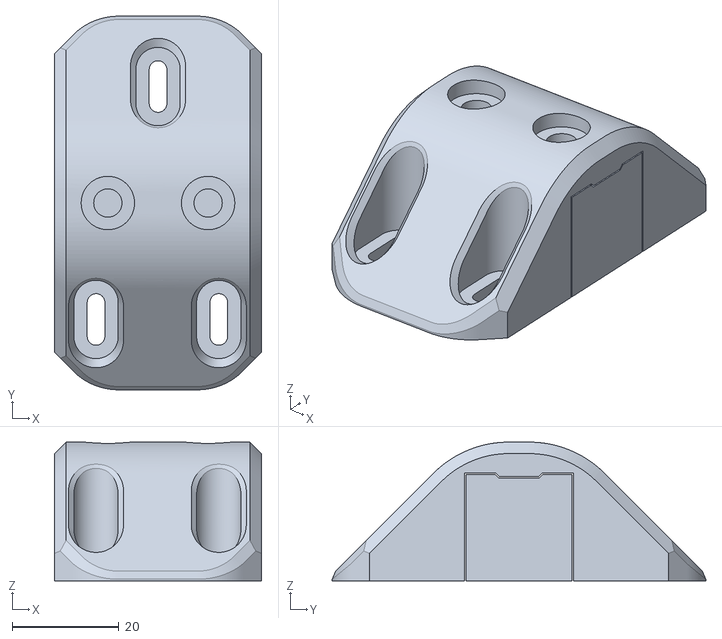
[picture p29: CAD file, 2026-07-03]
Kinematic 3Z - in progress/Toolhead/Dock_Mount_Main_x4.stl
38.8 x 70.0 x 26.0

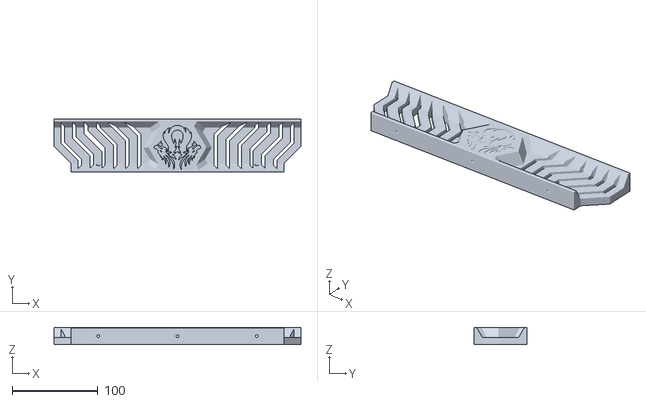
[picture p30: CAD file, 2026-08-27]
Kinematic 3Z - in progress/Base/Skirt_Front.stl
288.0 x 61.8 x 20.0

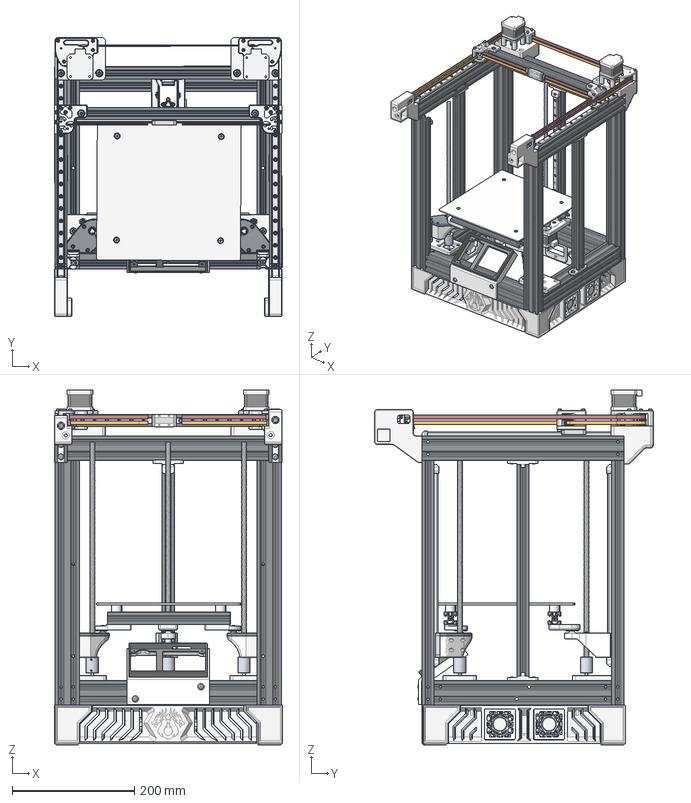
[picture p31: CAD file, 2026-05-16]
Kinematic 3Z - in progress/Duender3Z.step
373.1 x 455.1 x 579.8 mm
T-slot M5 x 41
HDMI5 Mount Main
Socket button head screw M5x0.8 x 8 x 97
HDMI5 mount frame
Leg_FL+BR x 2
Leg_FR+BL x 2
Side_Skirt_x2 x 2
Hex_Insert x 2
Front_Skirt
Plug_plate
Fan_grill x 4
Fan_Dummy_x4 x 4
Back_Skirt
Y brace
Top_spacer x 3
Z brace x 2
Y axis x 2
Bottom_spacer x 2
Z post x 4
Base F&B x 2
Base L&R x 2
M5 Insert x 18
Hex socket head cap screw M3x0.50 x 30 x 18 x 14
Hex socket head cap screw M3x0.50 x 8 x 94
Hex socket head cap screw M3x0.50 x 6 x 8
M3x30mm pin x 8
T-slot M3 x 54
2GT16T6W3B WITH teeth x 2
X_Carriage_Top_Right
M3 0,5mm shim x 39
MGN9 rail 300mm x 6
X_Carriage_Bottom_Left
2GT16T6W3B NO teeth x 10
M3 10mm spacer x 5
MGN9H carriage x 6
X_Carriage_Top_Left
X axis
X_Carriage_Bottom_Right
Hex socket head cap screw M5x0.80 x 25 x 2
Hex socket head cap screw M3x0.50 x 35 x 18 x 6
AB_Holder_Medusa_Right
F695-2RS x 2
Z Motor x 5
Hammerhead M3 x 2
AB_Tensioner_Right_Bottom
Socket button head screw M3x0.5 x 8 x 4
2GT16T6W6B Pulley x 2
AB_Tensioner_Left_Bottom
AB_Tensioner_Right_Top
M3x20mm pin x 2
Bottom_left_mount
Y_carriage_stopper x 2
Hex nut grade C M5x0.8 x 2
Belt R
AB_Tensioner_Left_Top
Belt L
Top_left_mount
Top_right_mount
Bottom_right_mount
AB_Holder_Medusa_Left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

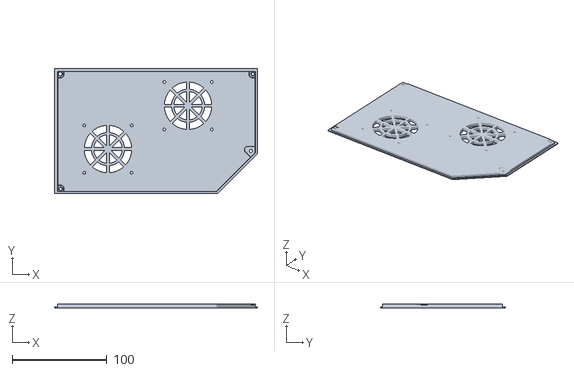
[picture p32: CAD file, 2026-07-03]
Kinematic 3Z - in progress/Extras/M8P Housing/M8P_eBox_Lid.stl
214.2 x 132.2 x 4.10

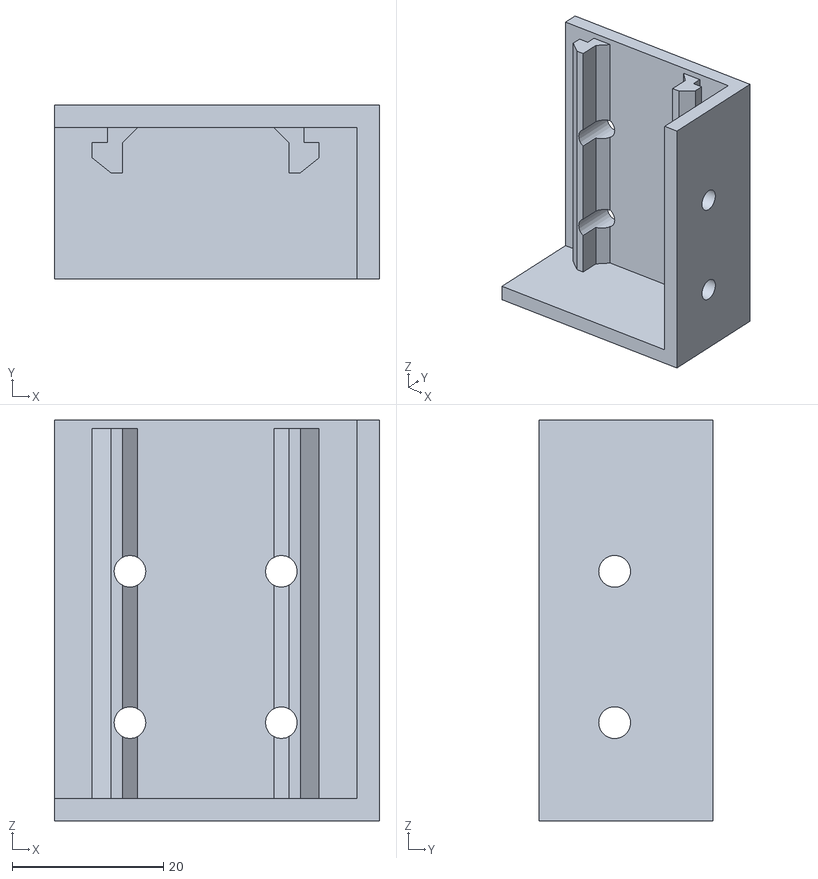
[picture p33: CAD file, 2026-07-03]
Kinematic 3Z - in progress/Extras/Tools/[t]_Blind_Joints_Drill_Jig.stl
43.0 x 23.0 x 53.0

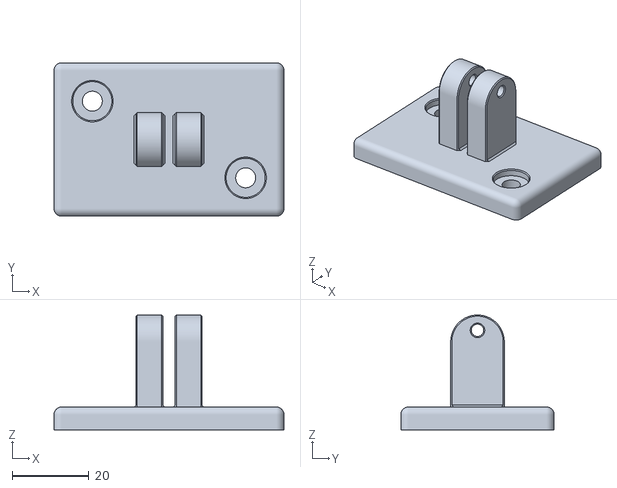
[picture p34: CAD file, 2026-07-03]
Kinematic 3Z - in progress/Screen/HDMI5_Base.stl
60.0 x 40.0 x 30.0

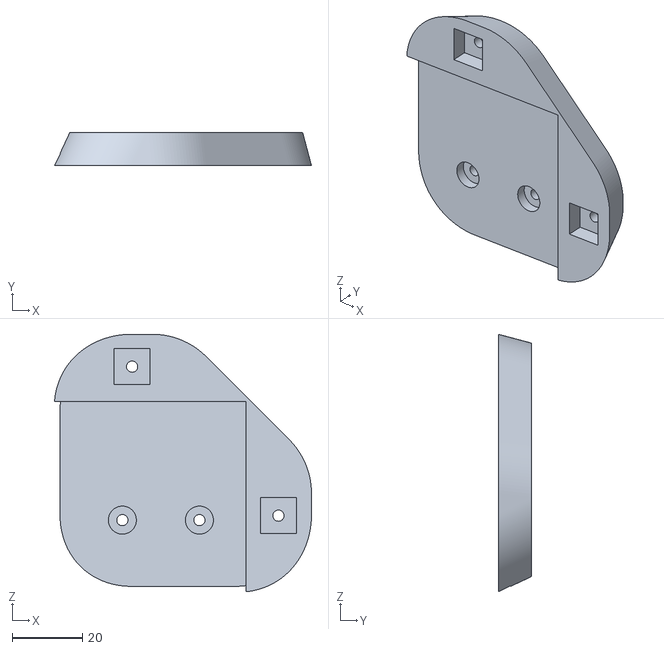
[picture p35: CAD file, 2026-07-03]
Kinematic 3Z - in progress/Sexball/Probe_Plate.stl
73.4 x 9.50 x 73.5

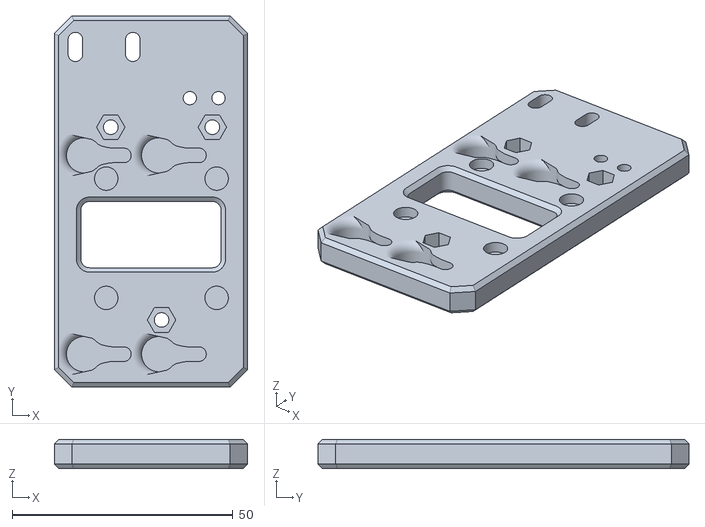
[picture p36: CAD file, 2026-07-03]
Kinematic 3Z - in progress/Toolhead/Dock_Mount_Plate_x4.stl
43.8 x 84.0 x 6.62

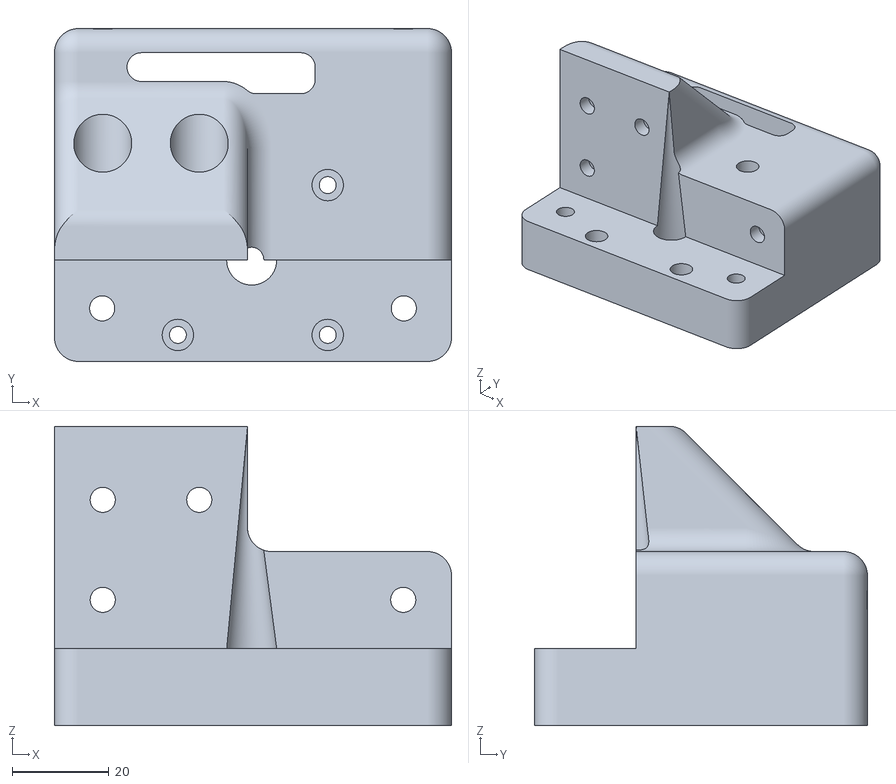
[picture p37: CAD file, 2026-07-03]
Kinematic 3Z - in progress/XY Axis/AB_Motor_Bottom_Right.stl
82.3 x 69.0 x 62.0

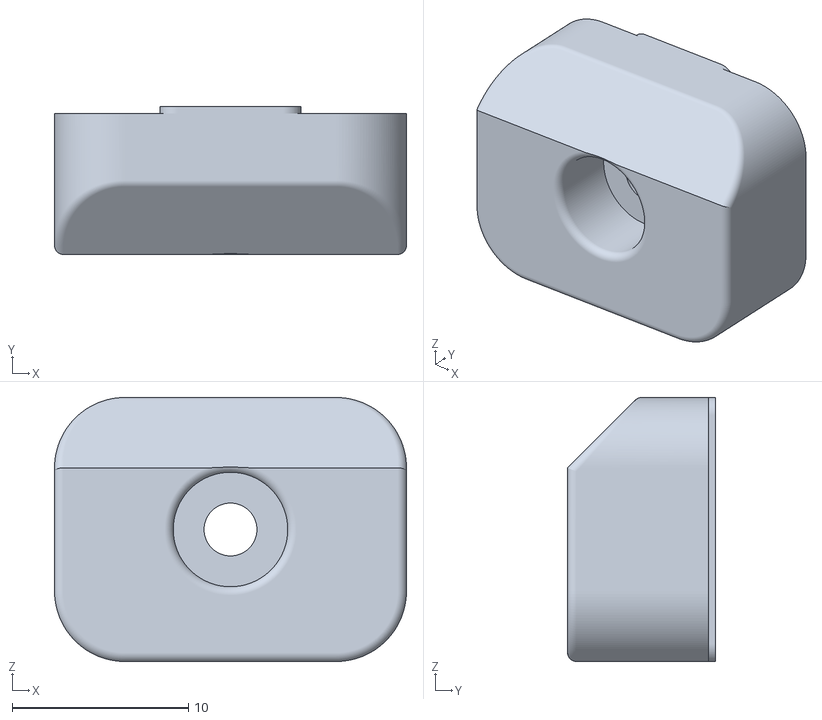
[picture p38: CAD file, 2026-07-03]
Kinematic 3Z - in progress/Z Axis/Z_Carriage_Stopper_x6.stl
20.0 x 8.40 x 15.0

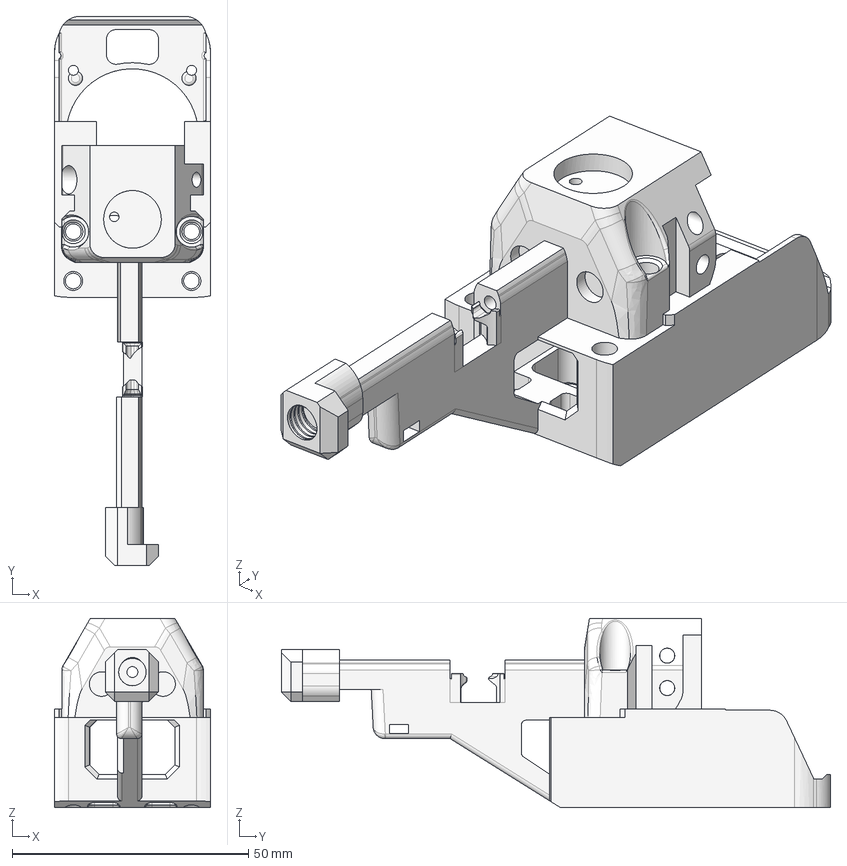
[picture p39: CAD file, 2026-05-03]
MedusaHC/Mirrored_Hotend_x4.step
33.0 x 116.2 x 40.0 mm

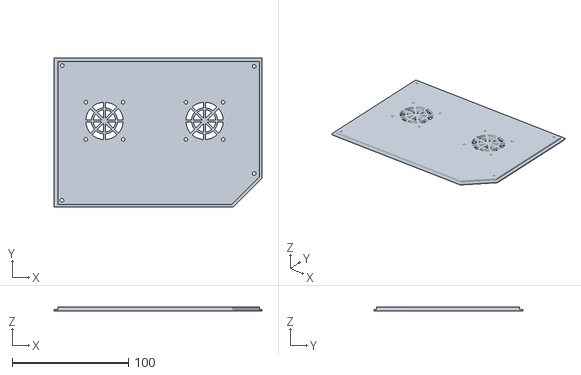
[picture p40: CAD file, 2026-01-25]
mods/Manta_Box_Cover_4010.stl
178.7 x 128.3 x 3.50

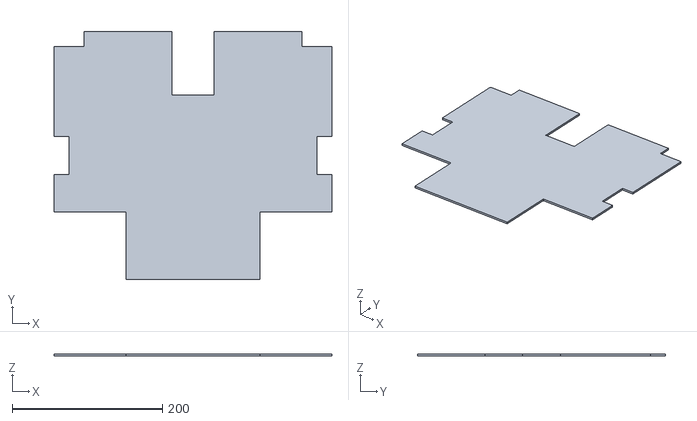
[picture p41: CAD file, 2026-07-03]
Kinematic 3Z - in progress/Base/_Base Cover.stl
370.0 x 330.0 x 3.00

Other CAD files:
Kinematic 3Z - in progress/Extras/M8P Housing/M8P_eBox_Case.stl
Kinematic 3Z - in progress/Extras/Tools/[t]_2020MGN9_Align_Tool_x2.stl
Kinematic 3Z - in progress/Screen/HDMI6_Frame.stl
Kinematic 3Z - in progress/Sexball/Bed_Clamp_x2.stl
Kinematic 3Z - in progress/Base/EMSgrill_Bolt_x14.stl
Kinematic 3Z - in progress/Base/EMSgrill_Foot_x8.stl
Kinematic 3Z - in progress/Base/EMSgrill_LRS_Mount.stl
Kinematic 3Z - in progress/Base/EMSgrill_M8P_Mount.stl
Kinematic 3Z - in progress/Base/EMSgrill_MountC.stl
Kinematic 3Z - in progress/Base/EMSgrill_MountD.stl
Kinematic 3Z - in progress/Base/EMSgrill_MountE_x22.stl
Kinematic 3Z - in progress/Base/Ems_Grill.stl
Kinematic 3Z - in progress/Base/Fan_Shrowd_x4.stl
Kinematic 3Z - in progress/Base/Leg_FL-BR_x2.stl
Kinematic 3Z - in progress/Base/Leg_FR-BL_x2.stl
Kinematic 3Z - in progress/Base/Skirt_Back.stl
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

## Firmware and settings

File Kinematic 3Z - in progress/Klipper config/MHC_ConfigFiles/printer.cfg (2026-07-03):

[include mainsail.cfg]
#[include Adaptive_Mesh.cfg]
[include Line_Purge.cfg]
[include macros.cfg]
[include sensorless.cfg]
[include timelapse.cfg]
[exclude_object]
#[include moonraker_obico_macros.cfg]
[include calibrate-offsets.cfg]

[include MHC_variables.cfg]

[include eddy_ng.cfg]
#[include eddy_ng_features.cfg]

#[include adxl.cfg]
#[include axiscope.cfg]
#[include bltouch.cfg]

[include toolchanger.cfg]

[gcode_arcs]
resolution: 0.1

[mcu CB2]
serial: /tmp/klipper_host_mcu

[mcu]
canbus_uuid: ec86e7529fab

[printer]
kinematics: corexy
max_velocity: 500
max_accel: 16000
max_z_velocity: 40
max_z_accel: 180
minimum_cruise_ratio: 0

[input_shaper]
shaper_type_x: ei
shaper_freq_x: 90.0
shaper_type_y: ei
shaper_freq_y: 80.6

[stepper_x]
step_pin: PE6
dir_pin: PE5
enable_pin: !PC14
microsteps: 32
rotation_distance: 39.8
endstop_pin: tmc2209_stepper_x:virtual_endstop
position_endstop: -10
position_min: -10
position_max: 250
homing_speed: 80
homing_retract_dist: 0

[stepper_y]
step_pin: PE2
dir_pin: !PE1
enable_pin: !PE4
microsteps: 32
rotation_distance: 39.8
endstop_pin: tmc2209_stepper_y:virtual_endstop
position_min: -59
position_endstop: 230
position_max: 230
homing_speed: 80
homing_retract_dist: 0

[stepper_z]
step_pin: PB8
dir_pin: !PB7
enable_pin: !PE0
microsteps: 128
rotation_distance: 8

#Bltouch or Eddy
endstop_pin: probe:z_virtual_endstop

#Regular Endstop
#endstop_pin: PF2
#position_endstop: 0

position_max: 240
position_min: -50
homing_speed: 25
homing_retract_dist: 0

[stepper_z1]
step_pin: PB4
dir_pin: !PB3
enable_pin: !PB6
microsteps: 128
rotation_distance: 8

#sensor_type:MAX31865
#sensor_pin: PA4
#spi_bus: spi1
#rtd_nominal_r: 100
#rtd_reference_r: 430
#rtd_num_of_wires: 2

#[filament_switch_sensor material_0]
#switch_pin: PC2


[heater_bed]
heater_pin: PF5
sensor_pin: PB1 # TB0
sensor_type: EPCOS 100K B57560G104F
control: pid
pid_Kp = 75.448
pid_Ki = 1.935
pid_Kd = 735.620
min_temp: 0
max_temp: 130

[fan]
pin: PA4

#[controller_fan driver_fan]
#pin: PC11
#stepper: stepper_x
#heater: extruder

[temperature_sensor MCU] 
sensor_type: temperature_mcu

[temperature_sensor CB2] 
sensor_type: temperature_host

#[temperature_fan CB2_fan]
#pin: !PC11
#sensor_type: temperature_host
#min_temp: 0
#max_temp: 90
#target_temp: 40.0
#control: watermark

[z_tilt]
z_positions:
    -8, 125
    243, 125
points:
    15, 100
    230, 100
speed: 150
horizontal_move_z: 2


[bed_screws]
screw1: 30.5, 37
screw2: 30.5, 207
screw3: 204.5, 207
screw4: 204.5, 37

#[heater_fan SoC_fan]
#pin: CB1:gpio79
#pin: RPI:gpio26

########################################
# TMC2209 configuration
########################################

[tmc2209 stepper_x]
uart_pin: PC13
run_current: 0.850
hold_current: 0.500
diag_pin: PF4
#driver_SGTHRS: 120
interpolate: True

[tmc2209 stepper_y]
uart_pin: PE3
run_current: 0.850
diag_pin: PF3
#driver_SGTHRS: 110
interpolate: True

[tmc2209 stepper_z]
uart_pin: PB9
run_current: 0.750
hold_current: 0.500
#diag_pin: PF2
interpolate: True
stealthchop_threshold: 999999

[tmc2209 stepper_z1]
uart_pin: PB5
run_current: 0.750
hold_current: 0.500
#diag_pin: PF1
interpolate: True
stealthchop_threshold: 999999

[tmc2209 extruder]
uart_pin: PG14
run_current: 0.800
hold_current: 0.300
#diag_pin: PC2
interpolate: True

#[tmc2209 extruder1]
#uart_pin: PA6
#run_current: 0.600
#diag_pin:

[autotune_tmc stepper_x]
motor: creality-42-40
#tuning_goal: silent
tuning_goal: performance
#extra_hysteresis: 4
sg4_thrs: 120

[autotune_tmc stepper_y]
motor: creality-42-40
#tuning_goal: silent
tuning_goal: performance
#extra_hysteresis: 4
sg4_thrs: 130

[autotune_tmc stepper_z]
motor: moons-c17hd2024n-01n
tuning_goal: silent
#tuning_goal: performance
[autotune_tmc stepper_z1]
motor: moons-c17hd2024n-01n
tuning_goal: silent
#tuning_goal: performance

[autotune_tmc extruder]
motor: biqu-35BYGF0713-A-10HZT
#tuning_goal: silent
tuning_goal: performance


########################################
# TMC2130 configuration
########################################

#[tmc2130 stepper_x]
#cs_pin: PD9
#spi_bus: spi2
#run_current: 0.800
#stealthchop_threshold: 999999
#diag1_pin: PD3

#[tmc2130 stepper_y]
#cs_pin: PD8
#spi_bus: spi2
#run_current: 0.800
#stealthchop_threshold: 999999
#diag1_pin: PD2

#[tmc2130 stepper_z]
#cs_pin: PB10
#spi_bus: spi2
#run_current: 0.650
#stealthchop_threshold: 999999
#diag1_pin: PC3

#[tmc2130 extruder]
#cs_pin: PB2
#spi_bus: spi2
#run_current: 0.800
#stealthchop_threshold: 999999
#diag1_pin: PC2

#[tmc2130 extruder1]
#cs_pin: PA6
#spi_bus: spi2
#run_current: 0.800
#stealthchop_threshold: 999999
#diag1_pin:

#[board_pins]
#aliases:
    # EXP1 header
 #   EXP1_1=PD5, EXP1_3=PB3, EXP1_5=PB5, EXP1_7=PB7, EXP1_9=<GND>,
 #   EXP1_2=PD4,  EXP1_4=PD6, EXP1_6=PB4, EXP1_8=PB6, EXP1_10=<5V>,
    # EXP2 header
 #   EXP2_1=PB14, EXP2_3=PB8, EXP2_5=PC10, EXP2_7=PC12,  EXP2_9=<GND>,
 #   EXP2_2=PB13, EXP2_4=PB9, EXP2_6=PB15, EXP2_8=<RST>, EXP2_10=<NC>
    
#[display]
#lcd_type: st7920
#cs_pin: EXP1_7
#sclk_pin: EXP1_6
#sid_pin: EXP1_8
#encoder_pins: ^EXP1_5, ^EXP1_3
#click_pin: ^!EXP1_2

#[output_pin beeper]
#pin: EXP1_1

#[display]
#lcd_type: uc1701
#cs_pin: EXP1_3
#a0_pin: EXP1_4
#rst_pin: EXP1_5
#contrast: 63
#encoder_pins: ^EXP2_5, ^EXP2_3
#click_pin: ^!EXP1_2

# See the sample-lcd.cfg file for definitions of common LCD displays.

#[bltouch]
#sensor_pin: PC13
#control_pin: PC15

# Proximity switch
#[probe]
#pin: PC15

#[neopixel my_neopixel1]
#pin: PC11

#[neopixel my_neopixel2]
#pin: PC14

#[adxl345]
#cs_pin: PC0
#spi_bus: spi2


[idle_timeout]
gcode:
  {% if printer.pause_resume.is_paused %}

    M118 Idle timeout while paused, turning off hotend

    SET_HEATER_TEMPERATURE HEATER=extruder TARGET=0

  {% else %}

    M118 Idle timeout

    TURN_OFF_HEATERS

    M84

  {% endif %}

timeout: 1200


#*# <---------------------- SAVE_CONFIG ---------------------->
#*# DO NOT EDIT THIS BLOCK OR BELOW. The contents are auto-generated.
#*#
#*# [bed_mesh default]
#*# version = 1
#*# points =
#*# 	0.388961, 0.361773, 0.203336, 0.095836, -0.106039
#*# 	0.417398, 0.360523, 0.203023, 0.087086, -0.099164
#*# 	0.384273, 0.296773, 0.176148, 0.020523, -0.122289
#*# 	0.500523, 0.423648, 0.289273, 0.160836, 0.012086
#*# 	0.521148, 0.452711, 0.331148, 0.213336, 0.031773
#*# x_count = 5
#*# y_count = 5
#*# mesh_x_pps = 2
#*# mesh_y_pps = 2
#*# algo = lagrange
#*# tension = 0.15
#*# min_x = 20.0
#*# max_x = 195.0
#*# min_y = 20.0
#*# max_y = 210.0
#*#
#*# [probe_eddy_ng btt_eddy]
#*# calibrated_drive_currents = 15
#*# calibration_version = 5
#*# reg_drive_current = 15
#*# tap_drive_current = 15
#*# calibration_15 = gASVywMAAAAAAAB9lCiMAXaUSwWMBGZ0b2iUjBtudW1weS5wb2x5bm9taWFsLnBvbHlub21pYWyUjApQb2x5bm9taWFslJOUKYGUfZQojARjb2VmlIwWbnVtcHkuX2NvcmUubXVsdGlhcnJheZSMDF9yZWNvbnN0cnVjdJSTlIwFbnVtcHmUjAduZGFycmF5lJOUSwCFlEMBYpSHlFKUKEsBSwqFlGgMjAVkdHlwZZSTlIwCZjiUiYiHlFKUKEsDjAE8lE5OTkr/////Sv////9LAHSUYolDUJ0oIr5ZVfY/VPOdr3Na/T+9IPvZTQfnP/IXKswCqOA/Wuw/CIPJzz/Lcjqa6xHKv8p1FJUm/LE/WaxgA/j63z8+wzPZwuOsP+s8hNa/6sS/lHSUYowGZG9tYWlulGgLaA5LAIWUaBCHlFKUKEsBSwKFlGgYiUMQDGVoF+3GlD4vAYT5PR6VPpR0lGKMBndpbmRvd5RoC2gOSwCFlGgQh5RSlChLAUsChZRoGIlDEAAAAAAAAPC/AAAAAAAA8D+UdJRijAdfc3ltYm9slIwBeJSMBnN5bWJvbJRoLHVijAlmdG9oX2hpZ2iUaAUpgZR9lChoCGgLaA5LAIWUaBCHlFKUKEsBSwqFlGgYiUNQfeLf2fLhGkAruV+USdsJQGL/MOuhV/o/gbRuq2iK9j9Pne6cprbvPyr0aERFbeG/AEeF6VDuvL/2SfXQ+576P1zZ0F99DuU/0Xn2MO552L+UdJRiaB1oC2gOSwCFlGgQh5RSlChLAUsChZRoGIlDEKxMrUdmG5U+Rwww32YvlT6UdJRiaCRoC2gOSwCFlGgQh5RSlChLAUsChZRoGIlDEAAAAAAAAPC/AAAAAAAA8D+UdJRiaCtoLGgtaCx1YowEaHRvZpRoBSmBlH2UKGgIaAtoDksAhZRoEIeUUpQoSwFLCoWUaBiJQ1Bn50PpRAeVPp9DcLvwRCI+REFmT1HgE75g197NJgoDPhD7fJBHS8+9CAyqU2cW+r3MJ3+hmJ7Nva/g32kc4v89WCTDYZUv0T3kA1bGNHHuvZR0lGJoHWgLaA5LAIWUaBCHlFKUKEsBSwKFlGgYiUMQALu47rCCPT/OqL2mr+8TQJR0lGJoJGgLaA5LAIWUaBCHlFKUKEsBSwKFlGgYiUMQAAAAAAAA8L8AAAAAAADwP5R0lGJoK2gsaC1oLHVijAdoX3JhbmdllF2UKEc/PYKw7ri7AEdALf/8K5bTVWWMB2ZfcmFuZ2WUXZQoR0FIKvisiXAAR0FIpH9ZHhAAZYwCZGOUSw91Lg==

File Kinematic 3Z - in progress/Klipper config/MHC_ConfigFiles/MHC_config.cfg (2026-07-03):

[pin_watch io]
  # Logical tool state (calculated from sensors)
  # -1 = head empty (all tools on bases)
  #  0..N-1 = tool on head (T0..T{N-1})
  # -2 = error / ambiguous sensor state
  sync_toolchanger: 0
  verbose: 0
  pin_e: ^!PF10
  pin_t0: ^!PF2
  pin_t1: ^!PF1
  pin_t2: ^!PF0
  pin_t3: ^!PC15
  debounce_delay: 0.0

[duplicate_pin_override]
pins: mcu:PF2, mcu:PF1, mcu:PF0, mcu:PC15, mcu:PF10, mcu:PG13, mcu:PG12, mcu:PG15

[extruder]
step_pin: PG13
dir_pin: PG12
enable_pin: !PG15
microsteps: 32
rotation_distance: 4.55
pressure_advance: 0.03
pressure_advance_smooth_time: 0.019
nozzle_diameter: 0.400
filament_diameter: 1.750
heater_pin: PA0 
sensor_pin: PB0 
sensor_type: ATC Semitec 104GT-2
control: pid
pid_Kp: 36.193
pid_Ki: 16.086
pid_Kd: 20.358
min_temp: 0
max_temp: 290
max_extrude_cross_section: 9999999
max_extrude_only_distance: 700
min_extrude_temp: 0
smooth_time: 2.0

[extruder1]
step_pin: PG13
dir_pin: PG12
enable_pin: !PG15
microsteps: 32
rotation_distance: 4.55
pressure_advance: 0.03
pressure_advance_smooth_time: 0.019
nozzle_diameter: 0.400
filament_diameter: 1.750
heater_pin: PA1
sensor_pin: PC5
sensor_type: ATC Semitec 104GT-2
control: pid
pid_Kp: 39.669
pid_Ki: 16.529
pid_Kd: 23.801
min_temp: 0
max_temp: 290
max_extrude_cross_section: 9999999
max_extrude_only_distance: 700
min_extrude_temp: 0
smooth_time: 2.0

[extruder2]
step_pin: PG13
dir_pin: PG12
enable_pin: !PG15
microsteps: 32
rotation_distance: 4.55
pressure_advance: 0.03
pressure_advance_smooth_time: 0.019
nozzle_diameter: 0.400
filament_diameter: 1.750
heater_pin: PA3
sensor_pin: PC4
sensor_type: ATC Semitec 104GT-2
control: pid
pid_Kp: 34.002
pid_Ki: 8.396
pid_Kd: 34.427
min_temp: 0
max_temp: 290
max_extrude_cross_section: 9999999
max_extrude_only_distance: 700
max_extrude_only_velocity: 150
min_extrude_temp: 0
smooth_time: 2.0


[extruder3]
step_pin: PG13
dir_pin: PG12
enable_pin: !PG15
microsteps: 32
rotation_distance: 4.55
pressure_advance: 0.03
pressure_advance_smooth_time: 0.019
nozzle_diameter: 0.400
filament_diameter: 1.750
heater_pin: PA5
sensor_pin: PA7
sensor_type: ATC Semitec 104GT-2
control: pid
pid_Kp: 28.904
pid_Ki: 12.846
pid_Kd: 16.258
min_temp: 0
max_temp: 290
max_extrude_cross_section: 9999999
max_extrude_only_distance: 700
min_extrude_temp: 0
smooth_time: 2.0

[gcode_macro T0]
gcode:
    RESPOND MSG="SET T0"
    SET T=0

[gcode_macro T1]
gcode:
    RESPOND MSG="SET T1"
    SET T=1
    
[gcode_macro T2]
gcode:
    RESPOND MSG="SET T2"
    SET T=2
   
[gcode_macro T3]
gcode:
    RESPOND MSG="SET T3"
    SET T=3



[servo my_servo]
pin: PE9
initial_angle:0

[heater_fan fan1]
pin: PF7
heater: extruder
heater_temp: 50.0

[heater_fan fan2]
pin: PF9
heater: extruder1
heater_temp: 50.0

[heater_fan fan3]
pin: PF6
heater: extruder2
heater_temp: 50.0


[heater_fan fan4]
pin: PF8
heater: extruder3
heater_temp: 50.0


[verify_heater extruder]
check_gain_time: 20
hysteresis: 10
heating_gain: 1

[verify_heater extruder1]
check_gain_time: 20
hysteresis: 10
heating_gain: 1

[verify_heater extruder2]
check_gain_time: 20
hysteresis: 10
heating_gain: 1

[verify_heater extruder3]
check_gain_time: 20
hysteresis: 10
heating_gain: 1

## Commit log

2026-01-09 Add files via upload
    Those are only cad outposts, they are NOT tested live yet. Anyone from the discord is welcome to do so.
    NOTE the left and right front joints, covers and supports are to be mirrored.
    9 M3x6 BHCS to hold the GE5C in place
    3 M5 nuts to insert in the LR and back joints
    2 round T8 lead screw nuts with their 4 M3x12 screws and 4 M3 nuts
    1 brass T8 lead screw nut with its 2 M3x12 screws and 2 M3 nuts
    3 GE5C bearings under each of the supports
    9 M3x6/8 SHCS or BHCS to secure the LR front joints covers
    12 M3x12 SHCS to attach the 3 joints to the MGN9H carriages
    5 M5x8 BHCS to attach the 3 supports under bed frame
    2 2020 200mm extrusions, fixed under the bed in place of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
    [Back Z - Bed support.stl, Front Z - LR Bed support.stl, Front Z - LR joint cover.stl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]
2026-01-25 Added MantaBox Lid for 4010 fans
    [Manta_Box_Cover_4010.stl]
2026-01-28 Added bottom Z brace spacer
    [Bed_holder-Back_support.stl, Bed_holder-Front_left_support.stl, Bed_holder-Front_right_suppot.stl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]
2026-01-28 Corrected printing orientation
    [Z_brace-Bottom_spacer.stl, Z_joints-Front_left_cover.stl, Z_joints-Front_left_joint.stl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]
2026-01-28 Added correct bottom Z spacer
    [Z_brace-Bottom_spacer.stl]
2026-05-03 Added mirrored MHC hotend
    [AdaptedAdapter_1.5mm.stl, AdaptedAdapter_1mm.stl, AdaptedAdapter_2mm.stl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]
2026-05-05 Updated kinematics (2-2.5Nm torque)
    [Bed_holder_Back.stl, Bed_holder_Left.stl, Bed_holder_Right.stl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]
2026-05-13 Z Axis Update
    [Bed_holder_Back.stl, Z_Joint_Front_Left.stl, Z_Joint_Front_Left_Cover.stl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]
2026-05-13 Need M5HexNut pocket
    [Z_Joint_Back.stl]
2026-05-14 Add readme with alignment and bed holder instructions
    Added detailed instructions for aligning the lead screw axis and bed holder adjustments to ensure proper movement and reduce stress.
2026-05-14 Update BOM of Duender3Z.csv
    [BOM of Duender3Z.csv]
2026-05-14 HDMI5 Screen housing
    [HDMI5_Mount_Main.stl, [a]_HDMI5_Mount_Frame.stl]
2026-05-16 Correction to front Z joints (M5heatsets)
    [BOM of Duender3Z.csv, Duender3Z.step, Z_Joint_Front_Left.stl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]
2026-06-10 Create Round cap - Part 1.stl
2026-06-11 BDI-22 upload
    [Round_cap_2.stl]
2026-06-11 Rm bdi
    [Round_cap_2.stl]
2026-06-13 Du 1st
    [printer.cfg]
2026-06-13 Create Config file
    [printer.cfg]
2026-06-13 Update eddy config
    [eddy.cfg]
